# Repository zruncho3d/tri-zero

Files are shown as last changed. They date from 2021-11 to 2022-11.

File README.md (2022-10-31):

# Tri-Zero - a triple-belted-Z V0 mod

a Voron Zero mod to add Automatic Bed Leveling - under $100, in only a few hours.

**Make every first layer perfect** and never adjust a bed screw again!  :tada:   

Upgrade your V0, or build a T0 from scratch with an augmented V0 kit.  

#### **Now with a Plus50 size, which adds 50mm X and Y travel, to 170mmx170mm:**

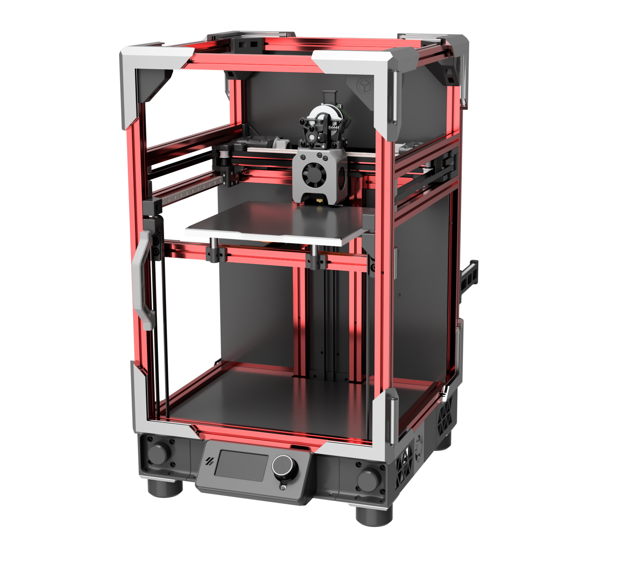
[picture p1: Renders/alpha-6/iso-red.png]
|  |
| - |
| T0 Plus50 with optional [BoxZero](https://github.com/zruncho3d/BoxZero) mod, Tecnologic-style [ZeroPanels](https://github.com/zruncho3d/BoxZero), and Mini 12864 display. |

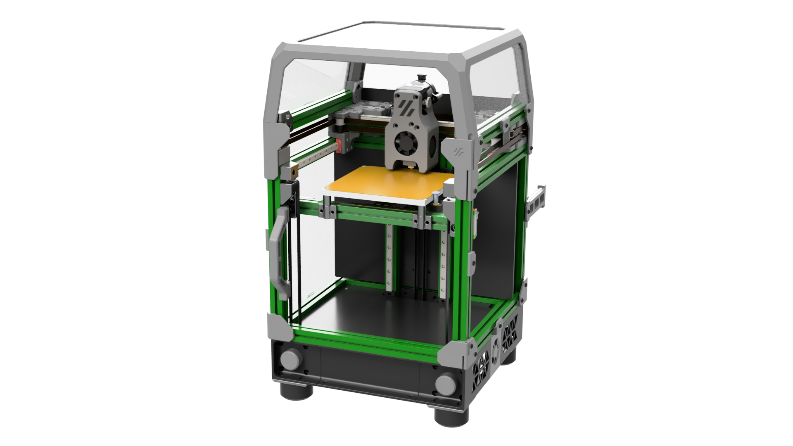
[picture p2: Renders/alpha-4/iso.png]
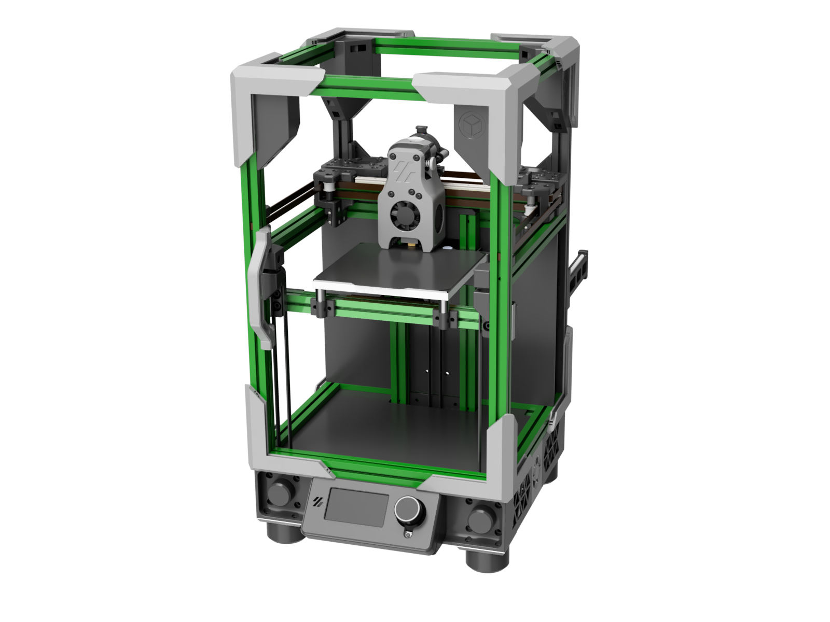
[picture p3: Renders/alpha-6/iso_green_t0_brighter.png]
|  | 
| - | - |
| T0 applied to V0 | T0 + [BoxZero](https://github.com/zruncho3d/BoxZero), [ZeroPanels](https://github.com/zruncho3d/BoxZero), & display.

### Why T0, vs other [Printers for Ants](https://3dprintersforants.com)?
* Less $, fewer failure points, and less potential for ringing than flying-gantry printers
* Faster Z motion compared to lead-screw printers, with no possibility of Z-banding
* Retains full space for electronics on the back
* Uses spare steppers you probably already have

*You don't even need to take the frame apart to do a V0 conversion.*

T0 is actively developed and community-supported, with over 20 builds completed, or in progress, as of October 2022.  Here are a few sample builds:

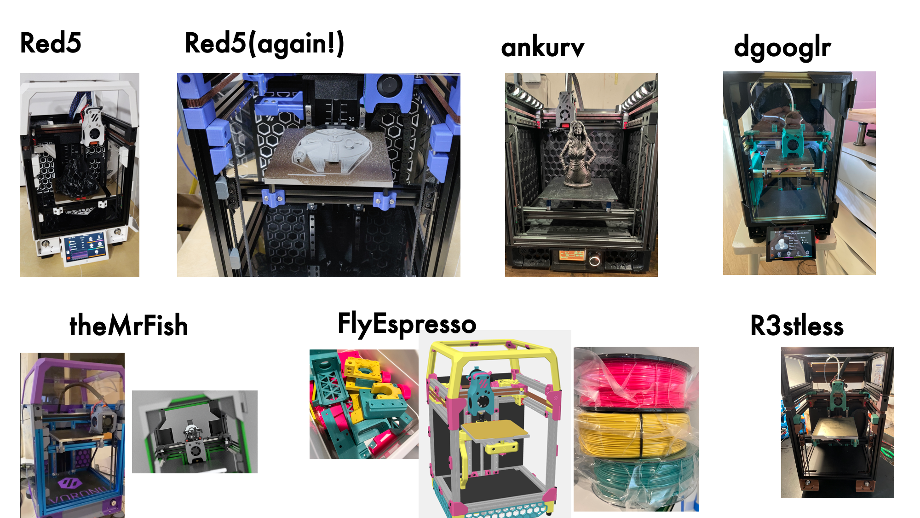
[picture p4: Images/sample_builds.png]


**Compatibility with the V0 ecosystem of kits, parts, and mods is a huge benefit**.

Plus, this mod pairs beautifully with the full family of Tri-Zero spinoffs:
* [BoxZero](https://github.com/zruncho3d/BoxZero) adds stability, easier sealing, and scalability for Plus50
* [ZeroPanels](https://github.com/zruncho3d/ZeroPanels) enables side panels to snap in/out in seconds, with an easy hinged top option
* [Dueling Zero](https://github.com/zruncho3d/DuelingZero) is a fully-boxed Tri-Zero with dual  gantries (!?!)

.. as well as [Double Dragon](https://github.com/zruncho3d/double-dragon), the IDEX V0 mod.

Join us on the [DoomCube Discord](https://discord.gg/doomcube) for any questions, comments, or just to see the latest dev activity.
*  Use `#tri-zero-forum` for support questions and build updates
*  Use `#tri-zero` for general chat and dev activity

Or, just straight to detailed docs:
- #### [Parts](PARTS.md): sourcing details
- #### [Instructions](INSTRUCTIONS.md): build steps, prep, and more
- #### [Plus50 size](PLUS50.md): sourcing and build notes for Plus50
- #### [FAQ](FAQ.md): Common questions, answered
- #### [Change](FAQ.md): Visual summary of past changes

## Overview and features

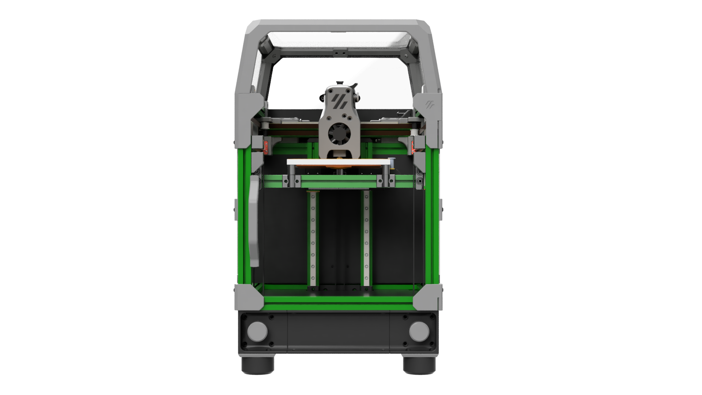
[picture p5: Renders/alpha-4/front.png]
Front
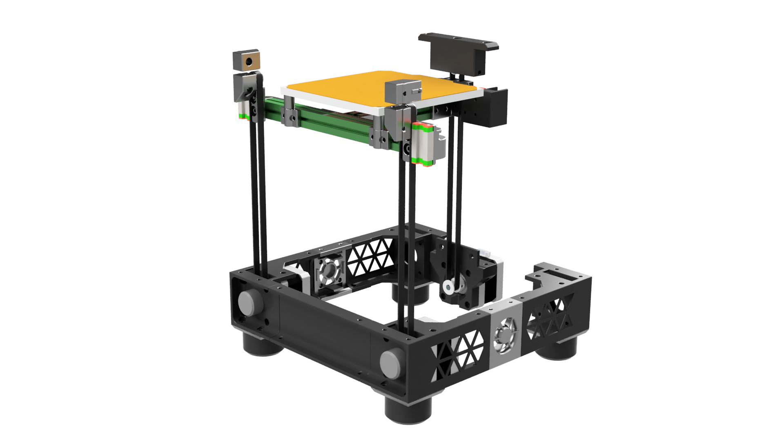
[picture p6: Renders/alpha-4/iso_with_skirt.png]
Iso with skirt
| Iso |  |   |
| - | - | - |

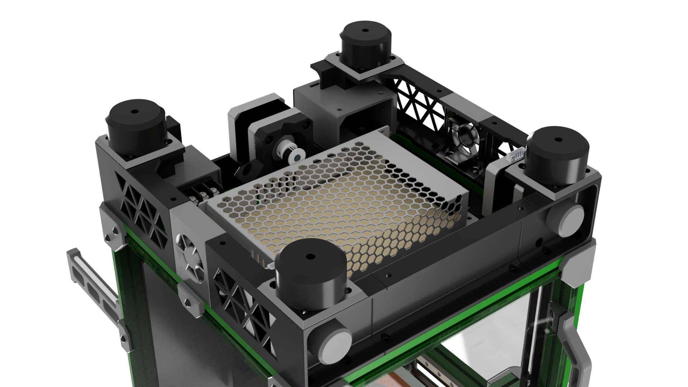
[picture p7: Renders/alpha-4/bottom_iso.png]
Bottom Iso
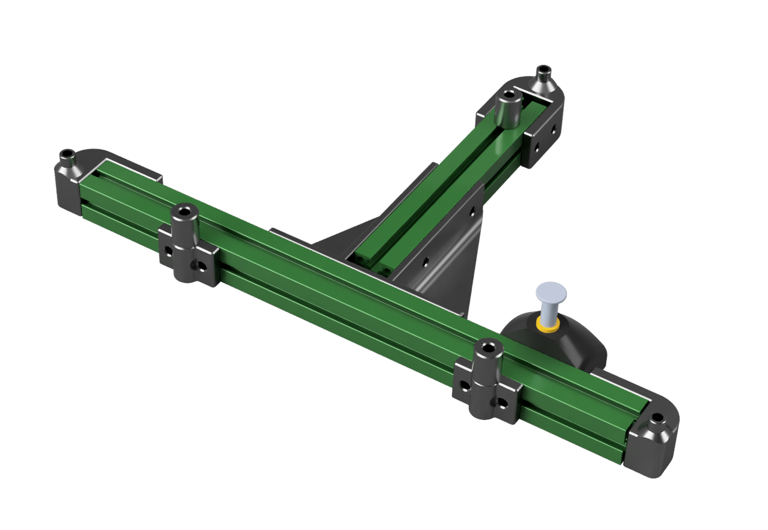
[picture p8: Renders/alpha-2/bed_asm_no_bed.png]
Bed Frame
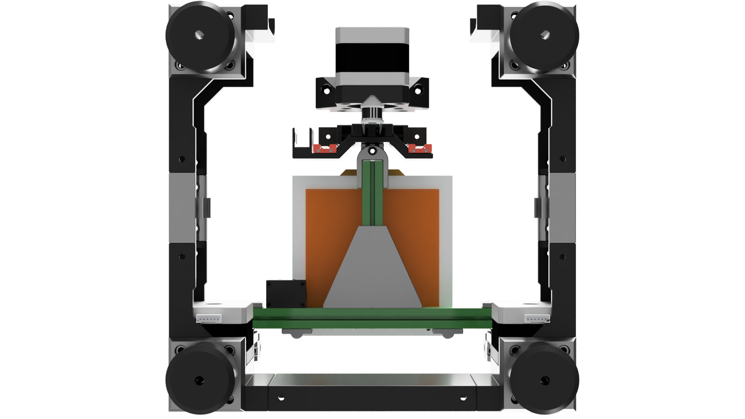
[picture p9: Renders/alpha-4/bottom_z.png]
Bottom Z
|  |  |  |
| - | - | - |

* Perfect Z layers, quiet motion, and great bed stability from 3 belted Z axes; no floppy cantilever here
* Reliable, stable Klicky-style bed probing with the [ZeroClick](https://github.com/zruncho3d/ZeroClick) detachable probe
* Optional rear endstop enables [automatic Z calibration](https://github.com/protoloft/klipper_z_calibration) and even auto-Z-offset for [IDEX](https://github.com/zruncho3d/double-dragon)
* Easy bed attachment and removal with built-in Wago mounts: 3 screws each
* Easy belt attachment and removal: fully tool-less
* Easy single-screw tensioning on all Z axes
* Easy to assemble: no hard-to-access screws or assembly-order nuances
* Your choice of display: 4.3" Touchscreen, Mini 12864, V0 Mini Display, or blank panel
* Supports large NEMA14 and mid-to-large NEMA17 Z motors
* Clean, minimal aesthetics with no-bridge, no-extreme-overhang parts

*This repo includes everything you need to build your own T0, including CAD and STLs for printed parts, as well as a list of parts:*

## Latest Release: Alpha-6

**There's never been a better time to deploy this mod.**

The community is growing.  20+ builds completed.  

With Alpha-6, the docs are vastly expanded and improved.  You can expect more good stuff to come, to make this mod  easier and faster to build.

**New in this release:**

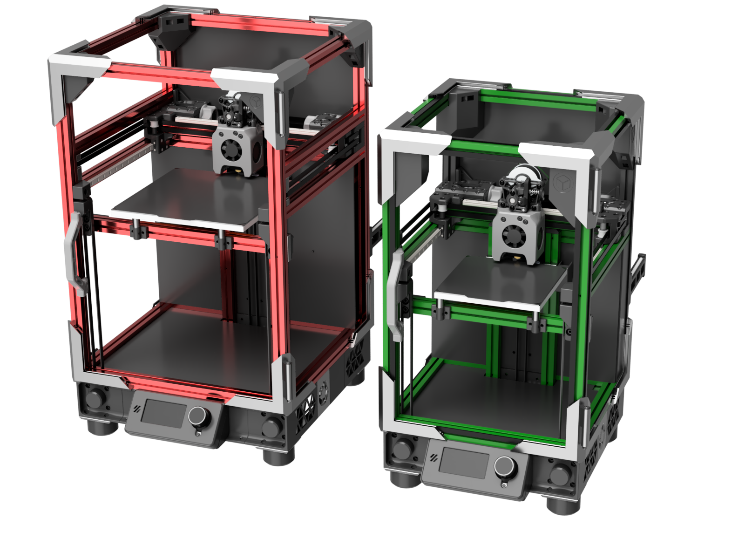
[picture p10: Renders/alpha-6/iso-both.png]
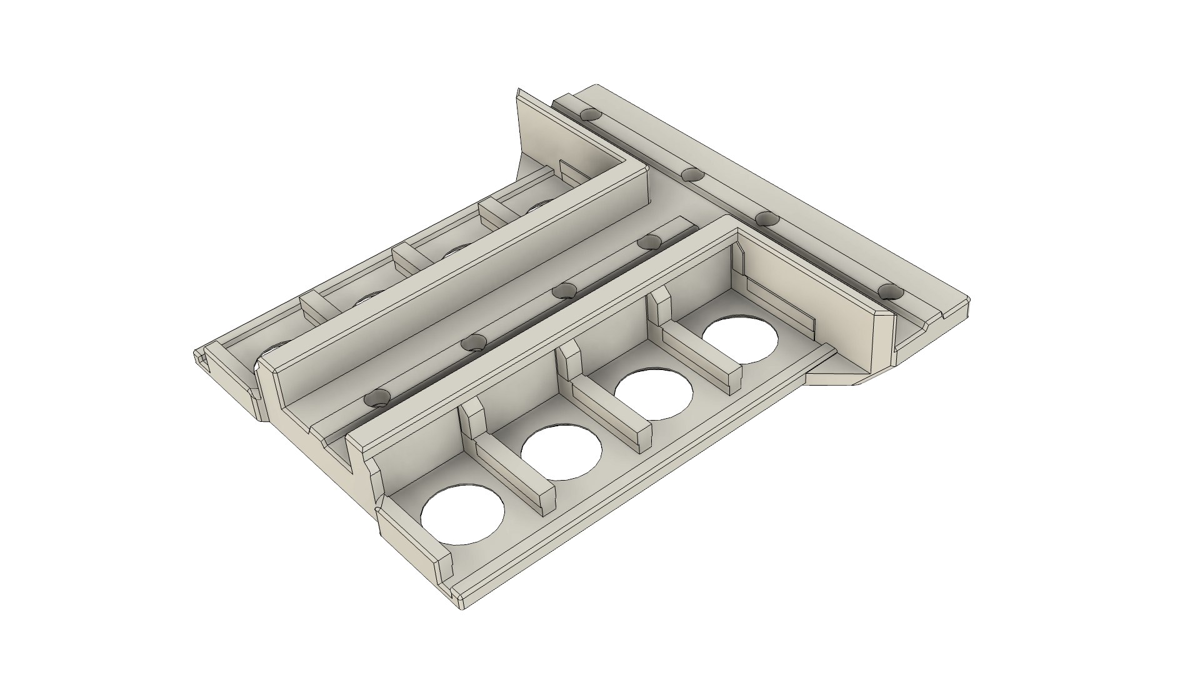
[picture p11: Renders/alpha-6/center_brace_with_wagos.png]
Iso with skirt
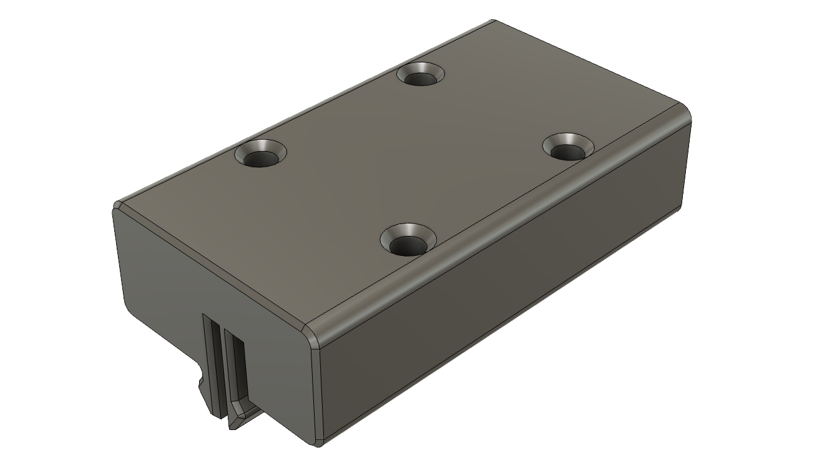
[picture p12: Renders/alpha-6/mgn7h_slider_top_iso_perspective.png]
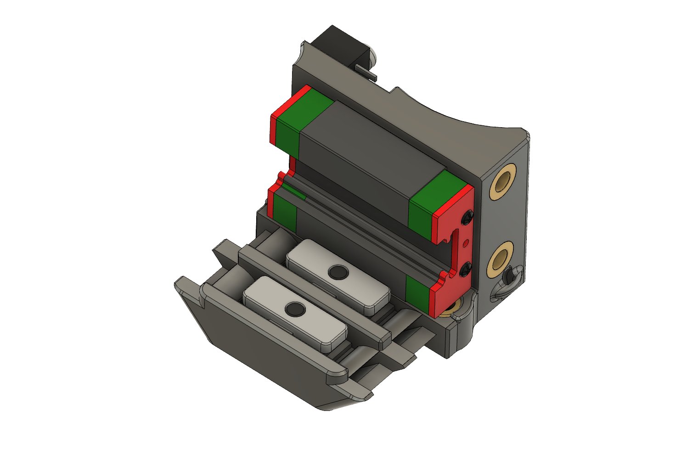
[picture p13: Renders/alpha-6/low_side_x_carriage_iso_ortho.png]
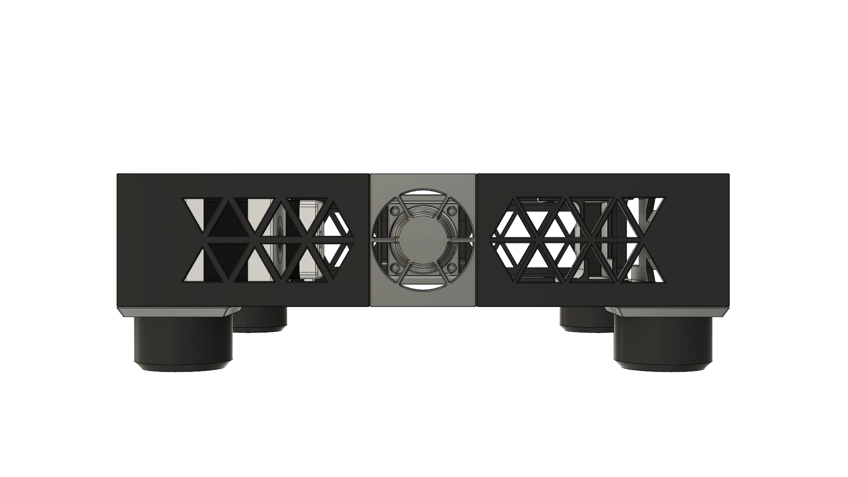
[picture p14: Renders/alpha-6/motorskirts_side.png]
Iso with skirt
|  |  |  |  |   |
| - | - | - | - | - |
| Plus50 Size | Integrated-Wago Bedframe | Rail-less Z Option | No-flush-cut carriages | 40mm Side Fans |

* **Plus50**, or **T0+** for short, is a new, larger, supported build size.  120x120 is good, but 170x170 is more usable, for little extra money.  T0+ can even be a cost-effective conversion for a V0, using 50mm extrusion chunks.  Shop the new [Plus Size](PLUS50.md) section for this year's newest model.

* **Bedframe with integrated Wago mounts**: Oh yes. The new "Connect 4" bedframe center makes bedframe attach/detach even easier, with up to 8 Wago connectors to support a bed heater, thermal fuse, optional AC ground, endstop, and thermistor wires.  Pop the Wagos in and out, toollessly.

* **Rail-Less Z Carriages**: Printed replacements for MGN7H rails that slide in an extrusion channel! Faster to install and saves money, too.  Used successfully on at least 4 builds at this point, including [Dueling Zero](https://github.com/zruncho3d/DuelingZero), so it's time to be more public about them.  *Currently considered experimental*, as the design is likely to change, and there is no long-term wear data on them.

* **No-flush-cut MGN9C carriage** Inspired by the [Double Dragon](https://github.com/zruncho3d/double-dragon) MGN9C mount; another T0 spinoff, first seen on [Dueling Zero](https://github.com/zruncho3d/DuelingZero).  No more one-time-use belts!

* **40mm fan skirt**: A potentially quieter option.

**Improved in this release:**

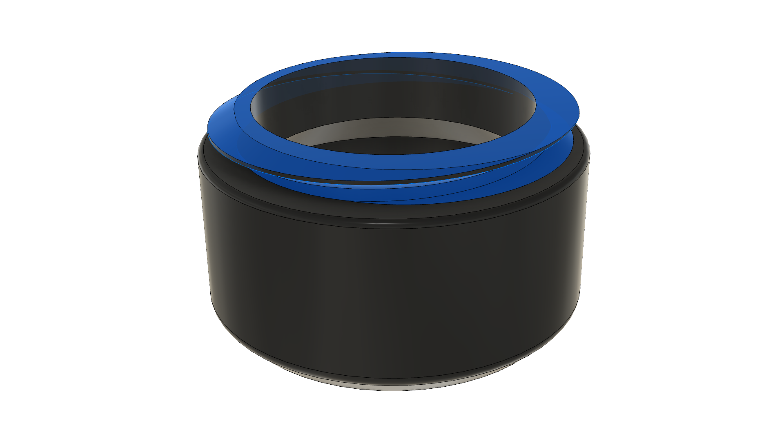
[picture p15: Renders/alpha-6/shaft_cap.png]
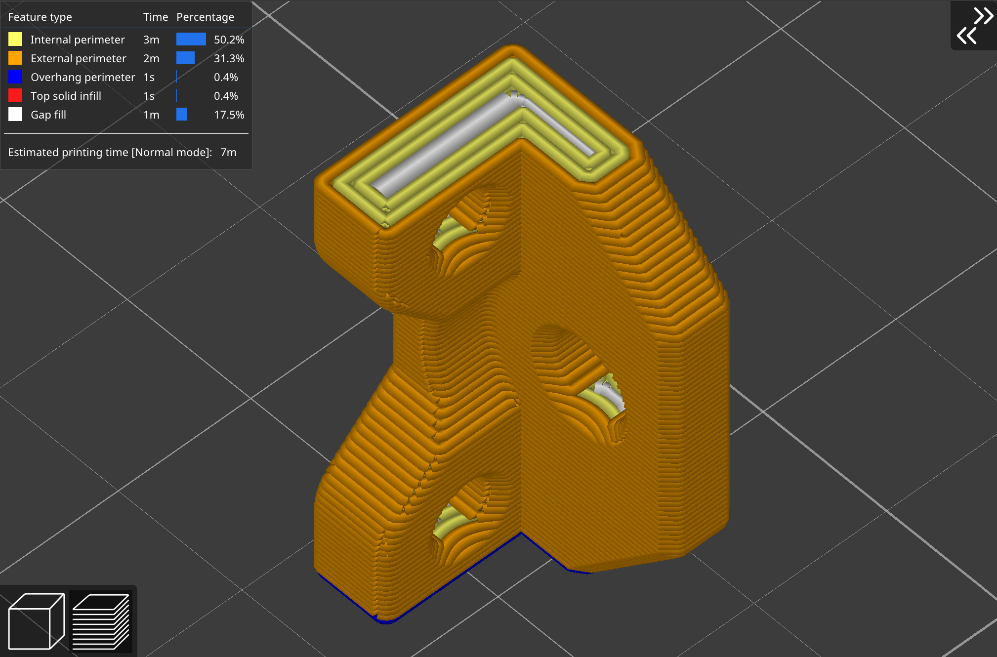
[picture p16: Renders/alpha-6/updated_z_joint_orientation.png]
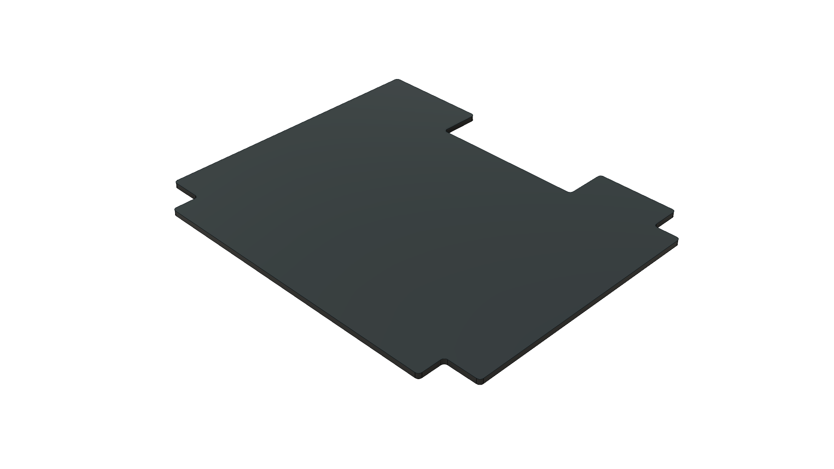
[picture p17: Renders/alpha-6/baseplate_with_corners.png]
Iso with skirt
|  |  |  | 600+ lines added! |
| - | - | - | - |
| Screw-in Shaft Caps | Updated Z joint orientation | Baseplate with corners | New docs all over |

* **Screw-in Shaft Caps**: These match updated MotorCorners; they'll never break now, with no clips in shear.  Much nicer.

* **Updated Z joint orientation**: Now printed vertically, to add strength in bending.  Should reduce the chance of breaking a $0.01 Z joint print upon head crashes.

* **Baseplate file with cutouts added**: Long-requested; saves the need to bust out your flush cutters or Dremel, if you're sourcing from scratch.

* **Docs**: Lots has been learned in the last year of T0, and now we have specific motor recommendations, config notes, tips, build steps, and an FAQ.  More visual, more engaging.  No proper manual yet, but this gets us halfway there.

Thanks to everyone who contributed to this release by testing parts!  You know who you are, and you'll get the ping-for-test again, I assure you :smile:.

I'm behind on reviewing GitHub pull requests, and that's up next: to make your mods more visible.

## Prior Changes

Prior changes (alpha-5, alpha-4, ...) are now noted in the **[visual changelog](CHANGES.md)**, which explains how T0 has evolved and walks through the interesting parts.

### Build Options: an Overview

No two builds are likely to be identical, and that's OK.  You're a smart, independent builder, and here you get to choose amongst the options to match your priorities and budget.  Next up is a quick overview, with the shared elements after.

#### Least-cost Stock-size Option: "starving student special" conversion - $0-$75

**Performs well, at minimum cost.**

Buy 3 small NEMA14 motors (< ~$30), print some sliders, and keep using your MGN7H X rail.  Buy some pulleys ($5), belt ($5), and fasteners ($10ish).  Buy a low-cost 2-4 driver board ($25).  Potentially $0 if you have the parts lying around from other printer, including magents and a switch for ZeroClick.  Sure, the rear bed joint might occasionally drop when the power cuts, and the sliders require a little bit of tuning, but once the printer rehomes, you're good, and the Z motion quality should match real rails.

#### Premium Model, 120x120: ~$110

**Performs the best.**

Might as well upgrade your X rail to MGN9C while you're at it ($15?), to  reduce toolhead flop.  Use beefy 48mm NEMA17s (~$45), and for rails, add one MGN7H to go with the one you just freed up ($15).  Otherwise the same.

#### Least-cost Plus50 BoxZero conversion: ~170x170: ~$150 to ~$200

You're also looking at a new K3-style or Prusa-Mini-style bed/magnet/flexplate ($35+), additional extrusion pieces ($30), new 200mm XY MGN7Hs and a 200mm MGN9C ($50), plus new longer XY belts ($10).  Yields a bit of extra Z travel too.

The price point is maybe $50 less if you're scratch-building and can leave out the Z rails, or you sell all the rails from your kit to someone who is scratch-building.  More details in the Plus50 section.

#### Premium Model, ~170x170: ~$200-$300

Move 4x MGN7H rails to Z, for ~130mm Z travel.

Optionally, add new clear ($20) and solid panels ($20).

Optinally, add a top-grade bed, like one from Mandala Rose Works meant for a Salad Fork.

Optionally, go for taller panels, taller BoxZero corners, custom frame, and 200mm MGN7H Z rails, to get a 170x170x170 build cube.

### Additional Credits / History

This printer is inspired by lessons learned while designing, building, and iterating on [F-Zero](https://github.com/zruncho3d/f-zero), a Voron Zero mod to add automatic calibration to a V0. Initial versions of T0 (alpha-1 and alpha-2) used F0 Z units with pulley reductions.  Now, T0 has moved to direct drive for Z, and the two designs now have almost no shared parts.

The [Buildlog Gdoc](https://docs.google.com/document/d/1kADhQN-p30GZuGi_6izB4IUN-McIifvLVtg8yTzIAgo/edit#) has historical details and links to early versions there.

The tensioner part derives from [MCMBen's Block-and-Tackle Z for V0](https://github.com/Fleafa/VoronUsers/blob/master/printer_mods/MCMBen/Voron0_Block_and_Tackle_Z_Belt/STLs/%5Ba%5D_tensioner_v1.stl) - Zruncho prints this vertically for clean surfaces, but make sure you have good layer adhesion.

The 4.3" Waveshare Touchscreen mount is based on Jeoje's great Voron2.4 [Touchscreen mod](https://github.com/VoronDesign/VoronUsers/tree/master/printer_mods/jeoje/4.3_Inch_Touchscreen_Mount).

The Mini 12864 Display mount is based on Gola's [V0 Trident Skirt Mix](https://github.com/VoronDesign/VoronUsers/tree/master/printer_mods/golas/v0-trident-skirt-mix).

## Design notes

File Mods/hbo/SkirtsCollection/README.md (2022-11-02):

# Collection of Tri-Zero Skirts

This is a Collection of skirts for the try-zero with some additional features.

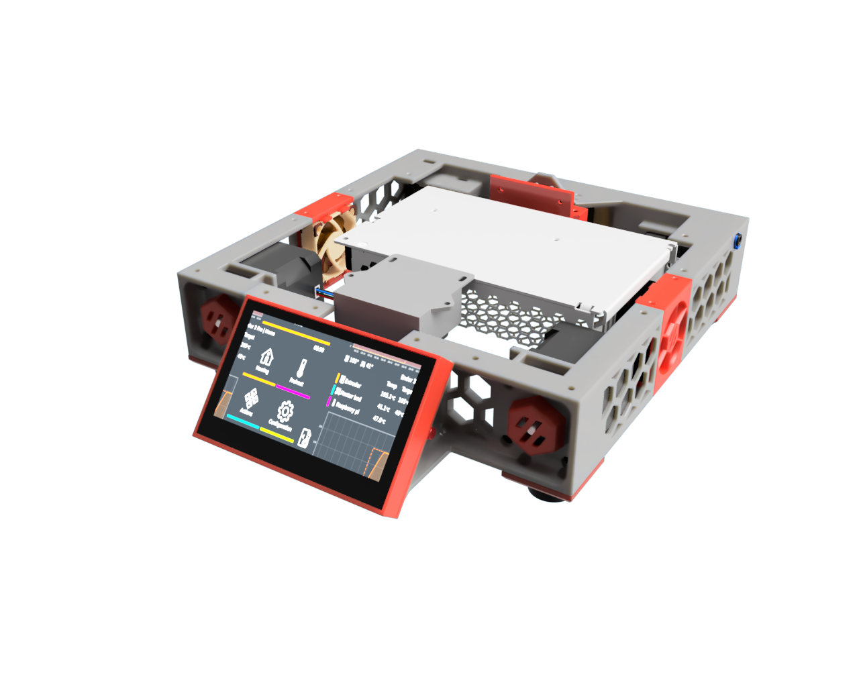
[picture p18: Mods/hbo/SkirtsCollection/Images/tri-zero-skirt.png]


Right now, there are 2 variations for the skirts and one common rear and common fan mounts.
To start with the rear ..

## Rear Skirts

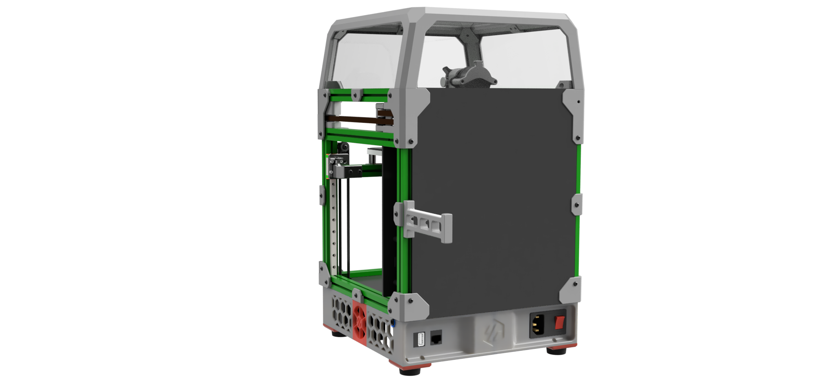
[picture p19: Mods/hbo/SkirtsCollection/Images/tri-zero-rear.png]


The rear skirts match all the different front skirts and have the following features

- integrated power inlet mount. To be used with the "standard" v0 power inlet
- 2 keystone mount points to get access to the raspberry pi ports
- Bowden clip mount point. Designed for the E3D style bowden clips. This allows to push the filament and not the tube from the outside. Read for the ERCF :)

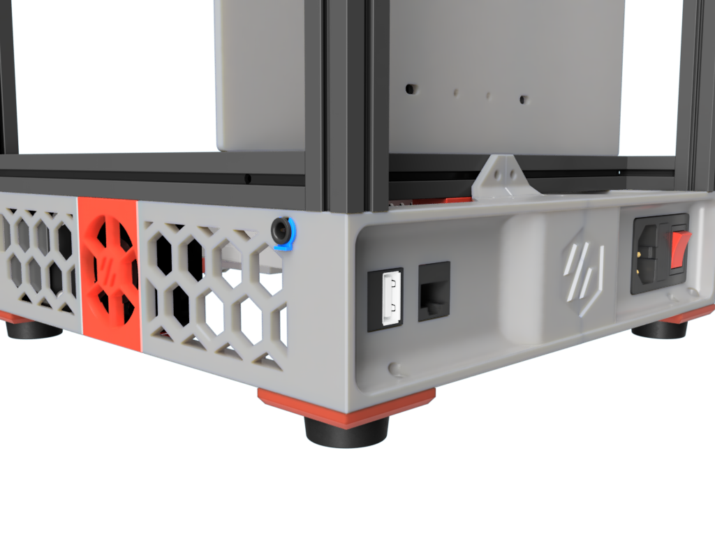
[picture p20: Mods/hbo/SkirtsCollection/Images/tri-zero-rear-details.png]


## Fan Mounts

Option: The fan mounts have clips to hold 40x10mm or 40x20mm fans.
If you go with a 20mm fan make sure to order one with a central rib, like the fans from creality.

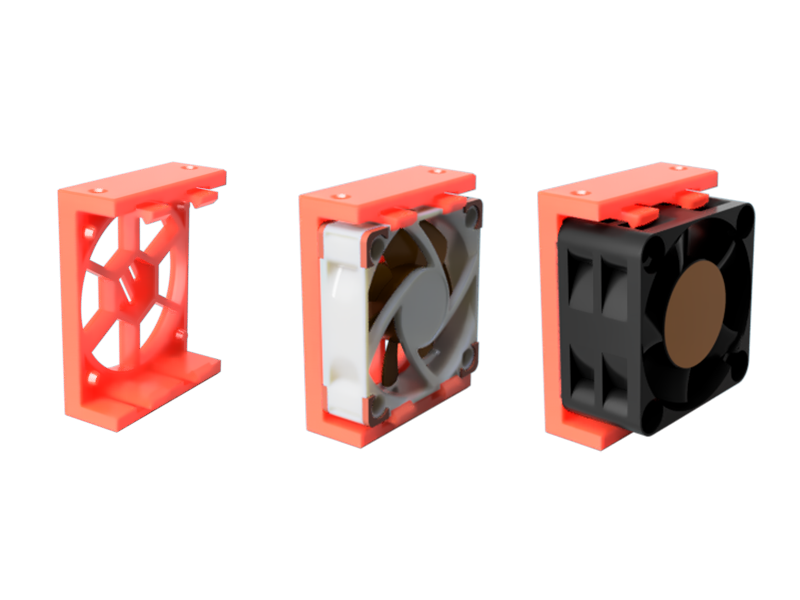
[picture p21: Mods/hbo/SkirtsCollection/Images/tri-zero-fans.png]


# Skirt Options

The front skirts are designed for Nema 17 motors up to a max size of 39 mm in length.

Note that there are two front covers for the GT2 pulleys. One for NEMA's with a shaft of 20mm and one for NEMA's with a 24 mm shaft.

## 1. Headless

This version is intended for users that like to run the tri-zero in headless mode i.e. without display

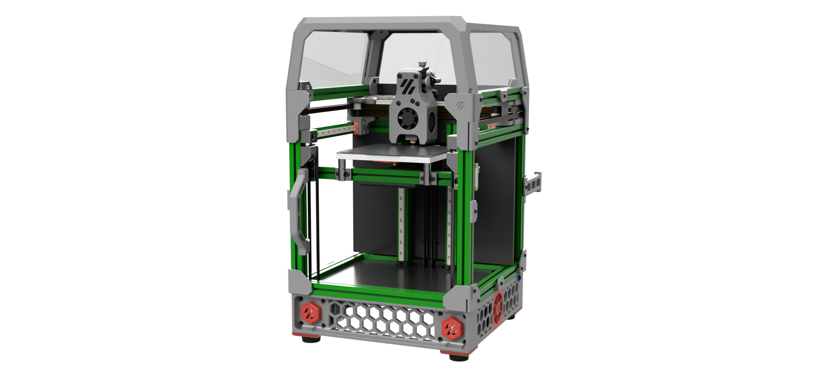
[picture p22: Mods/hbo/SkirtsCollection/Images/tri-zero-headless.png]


## 2. Waveshare 4.3" Display

This version is designed for the Waveshare 4.3inch Capacitive Touch Display for Raspberry Pi, DSI Interface
The mounts are designed to bolt on the frame and display with original screws from the back.
Therefore similar 4.3 inch display might not work without modifications
I'm using a 60cm DSI cable to connect the display with a Raspberry PI back on the back of the V0 
(a Raspberry Pico mount mod is in preparation)

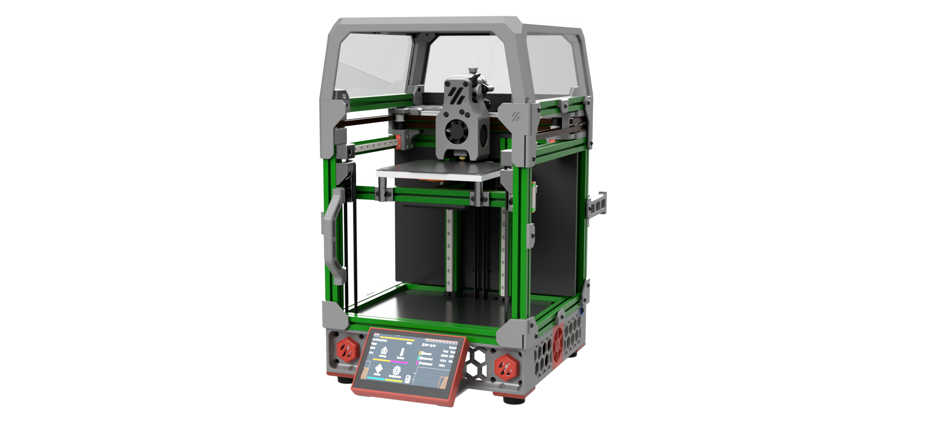
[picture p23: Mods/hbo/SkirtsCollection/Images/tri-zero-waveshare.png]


### Reset / Emergency switch
The front display mount also provide a mounting option for a reset or emergency switch.
I'm using this switch to reset a BTT PSU relays. 

The switch in the cad is a standard 7mm momentary switch that is easy to source even from local providers.
Make sure to get a Normaly OPEN (NO) switch if you plan to use it with the BTT PSU Relays.
(A Relays mount and firmware configs are in preparation)

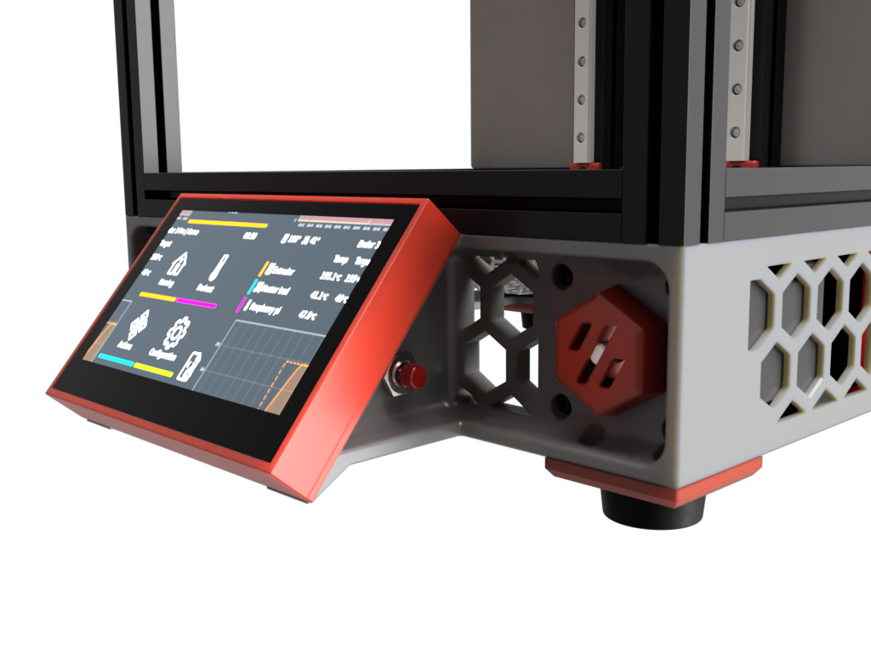
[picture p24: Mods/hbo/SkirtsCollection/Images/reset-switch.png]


# Printing

This mod is based on my design for the V0 and Double Dragon / Wasp printer.
The core design went to many iterations (and spools of filament) to optimize printability and tolerances for keystones, power inlets etc.

I printed the motor corners to check the design but I have not yet built a printer with them. So please provide feedback if you run into issues or confirm the design.

All parts print with standard Voron print setting without any supports.
All parts fit on a V0. However, the max out the build volume on the z axis.
If you need to print on a V0 make sure that your bed springs are really stiff by adding more tension with washers etc.
I had some problems getting nice parts out of the V0 due to the nozzle moving the part due to flex on the bed springs.

# BOM Notes

Recommended Nema 17 Motor: https://www.omc-stepperonline.com/de/nema-17-bipolar-1-8deg-26ncm-0-4a-0-4a-12v-42x42x34mm-4-draehte-17hs13-0404s1

Waveshare Display:  https://www.waveshare.com/4.3inch-dsi-lcd.htm

Rubber Feet: There are many options. The one in the CAD are these ones here https://de.aliexpress.com/item/1005004478863418.html

7mm Momentary switch:  https://de.aliexpress.com/i/32711341102.html

40x20mm fan:    https://de.aliexpress.com/item/1005002920453385.html

# CAD  Notes

The CAD includes all variants in one file.
You need to show/hide the version you like to work with

# Credits

Thanks to zruncho for all his efforts he puts into the printers for Ants.
It's inspiring for a lot of us!

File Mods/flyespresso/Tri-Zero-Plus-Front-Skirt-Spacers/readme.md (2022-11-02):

# Tri-Zero Plus: Front Panel Spacers
#### _For Tri-Zero Plus! Not needed for standard/V0 conversions_

This is a simple additional flair piece for the front, that will cover any gaps for whatever front you choose, i.e. waveshare as shown below. Blue highlights the additional pieces.

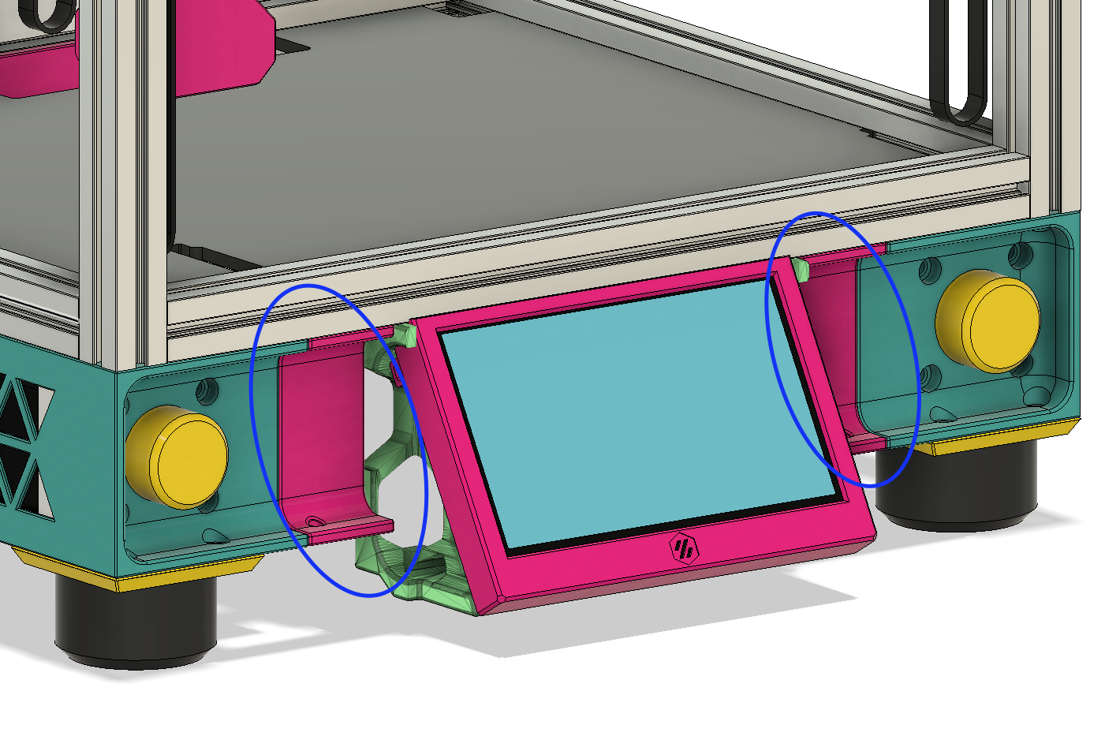
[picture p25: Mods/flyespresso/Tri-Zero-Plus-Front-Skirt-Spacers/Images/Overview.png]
Overview


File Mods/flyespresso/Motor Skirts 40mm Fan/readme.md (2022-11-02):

# 40mm Fan Motor Skirt Adapters
## _For Tri-Zero & Plus!_
This mod is made with Noctua 40mm fans in mind but should work for any 40mm fans, requires inserts.

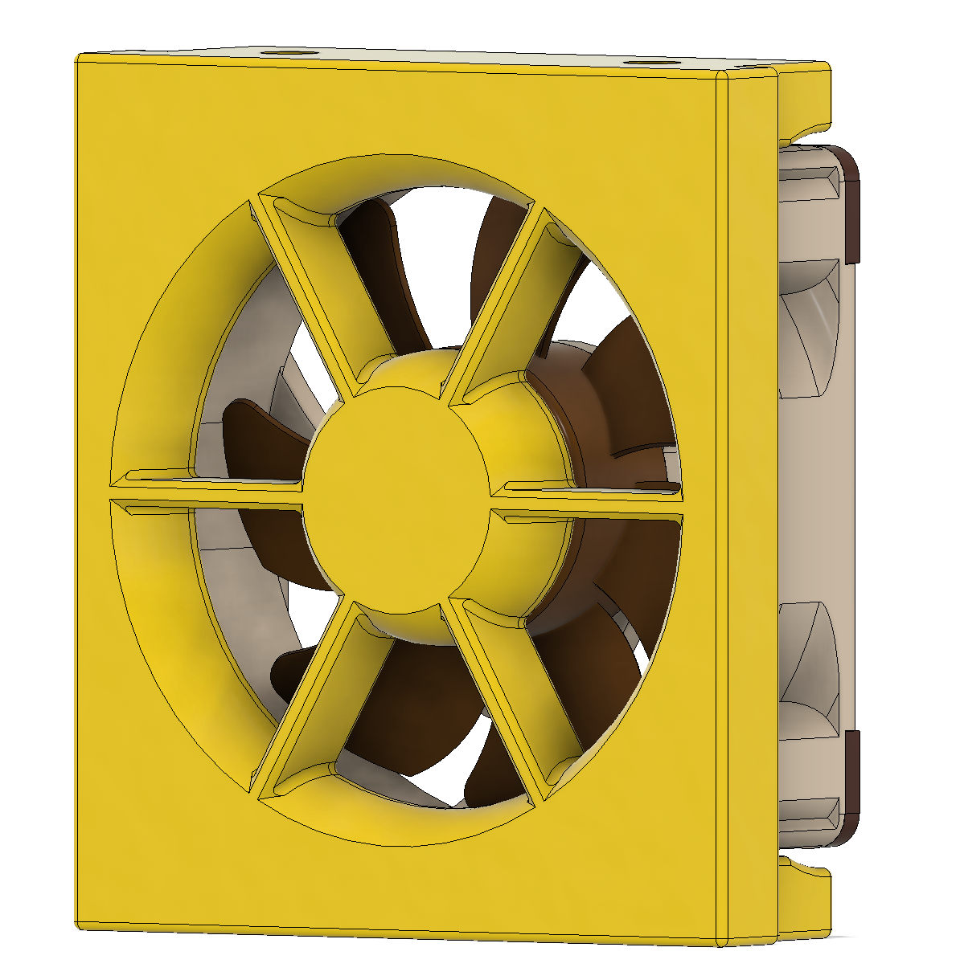
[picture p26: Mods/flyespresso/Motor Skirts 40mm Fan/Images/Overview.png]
Overview

Note that the holes to connect to the frame have a little overlap to the main body--that's fine as you can push the screw past that and then it acts like a captive screw. This way lot easier to instal! It's in the below images in Green. Red is where you will need heat sets (x4) per fan. See here:

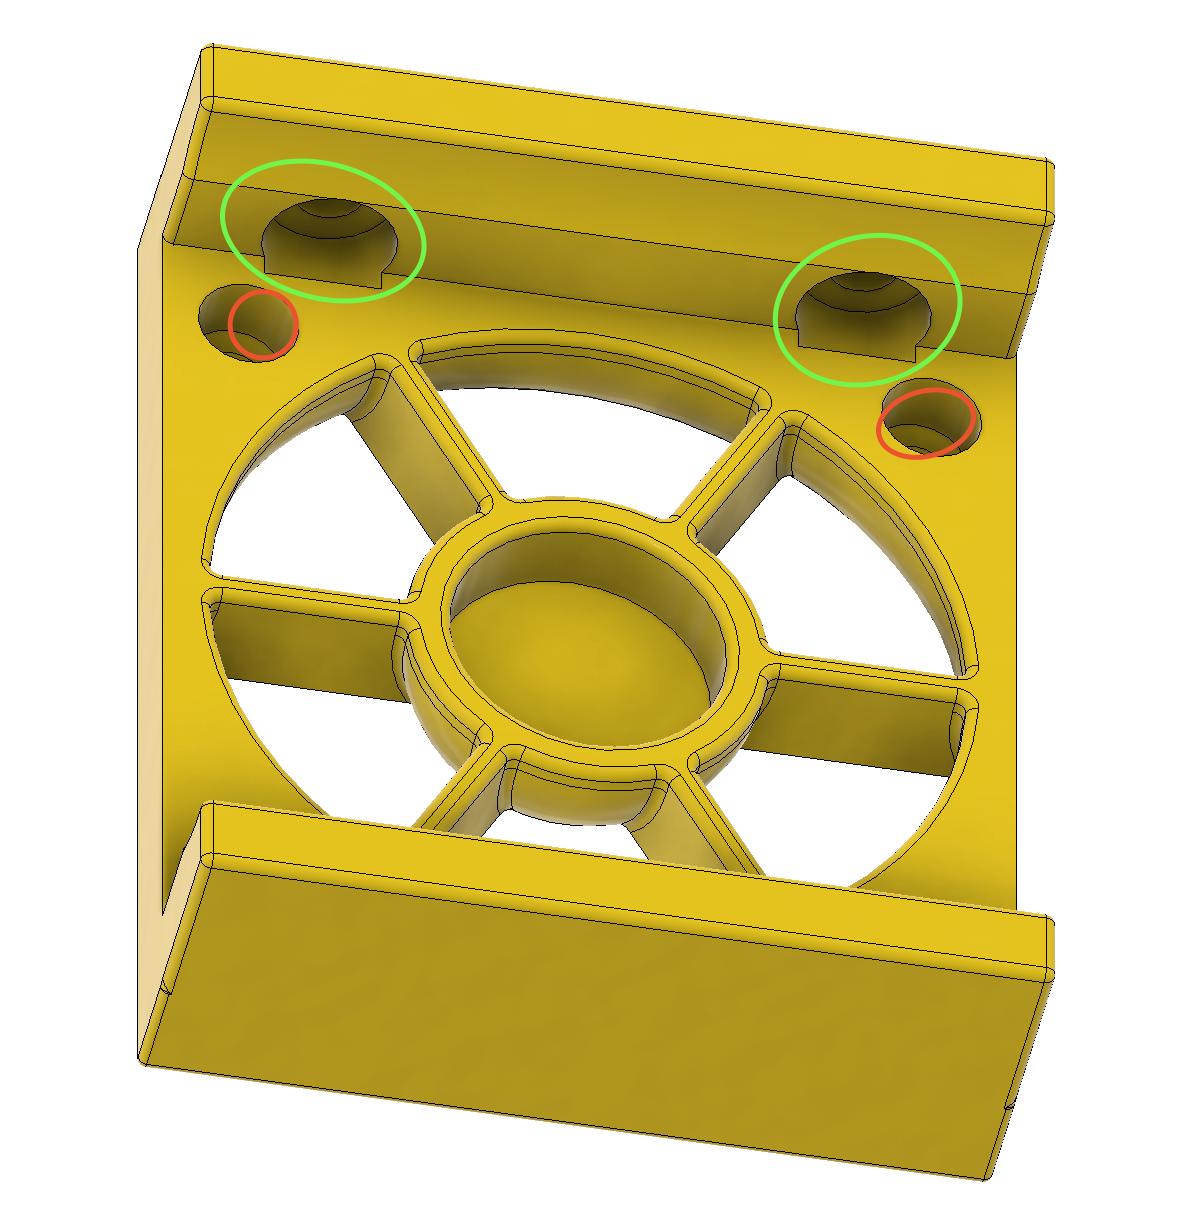
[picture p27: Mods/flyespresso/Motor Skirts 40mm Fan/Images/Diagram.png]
Diagram


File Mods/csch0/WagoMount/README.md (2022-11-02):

# Overview

Attach Wago 221-412 to your tri-zero bed.

Idea taken from this mod for the v0: https://github.com/VoronDesign/VoronUsers/tree/master/printer_mods/deepfriedheroin/v0_bed_wagos

## BOM
* 1x M3 8mm
* 1x M3 Nut
* 4x M3 6mm
* 4x M3 Heat inserts (from the V0 BOM)
* 6x Wago 221-412

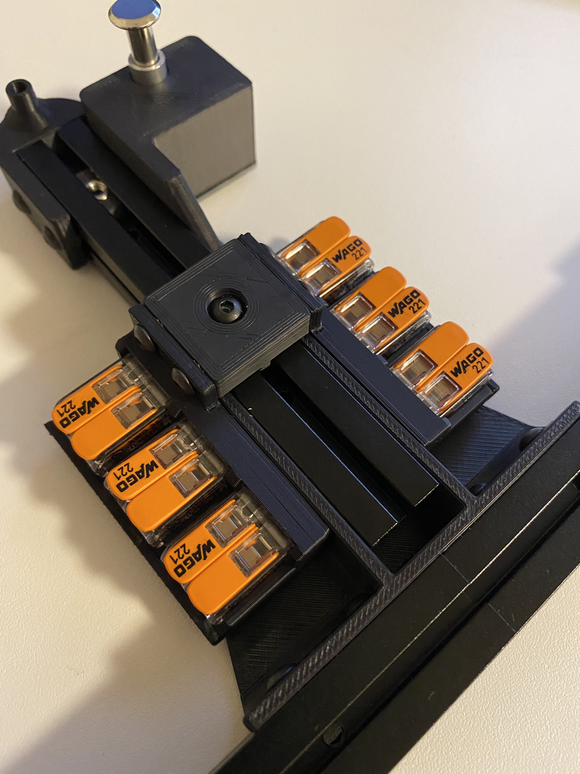
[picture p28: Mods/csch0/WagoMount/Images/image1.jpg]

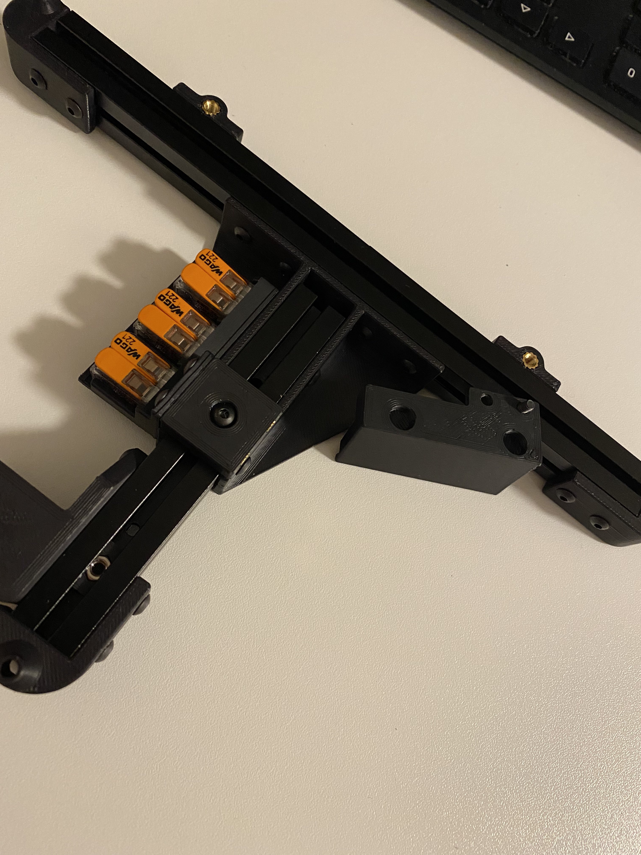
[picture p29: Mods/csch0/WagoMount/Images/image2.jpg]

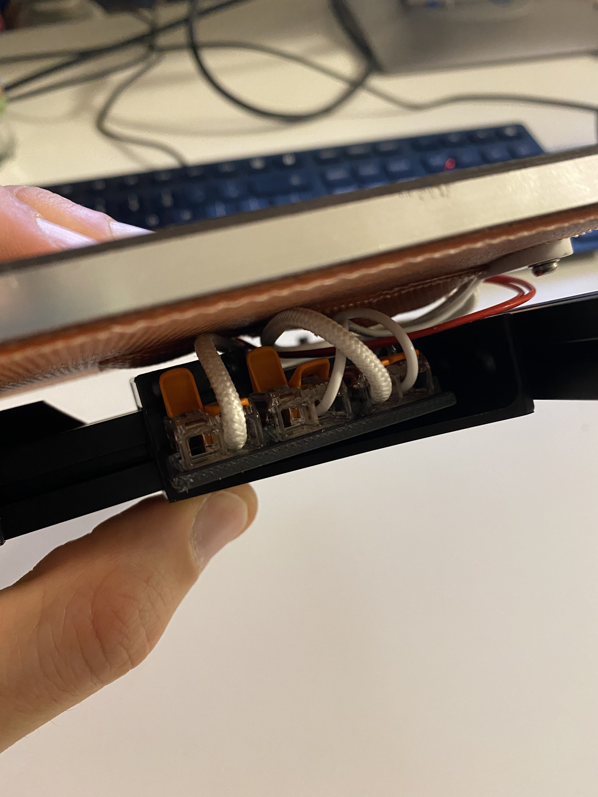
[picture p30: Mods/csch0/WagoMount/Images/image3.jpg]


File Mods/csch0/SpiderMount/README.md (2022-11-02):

# Overview

Mount for the spider mainboard, supports the [Wire Fingers](https://github.com/zruncho3d/double-dragon/blob/main/STLs/Optional/Wire_Fingers_x6.stl) created by [zruncho3d](https://github.com/zruncho3d).

## BOM
* 4x M3 6mm
* 2x M3 8mm
* 6x M3 Heat inserts (from the V0 BOM)
* 6x [Wire Fingers](https://github.com/zruncho3d/double-dragon/blob/main/STLs/Optional/Wire_Fingers_x6.stl)

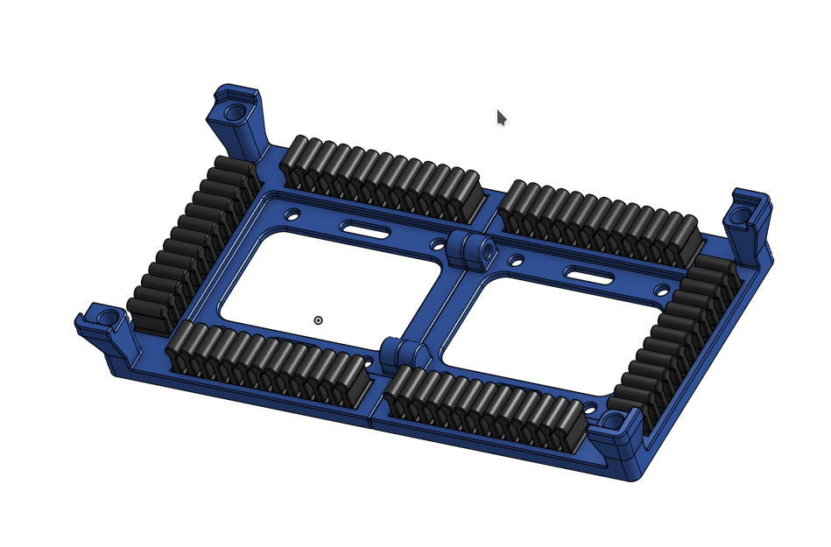
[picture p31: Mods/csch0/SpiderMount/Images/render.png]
render


Installed it looks like this on my tri-zero.

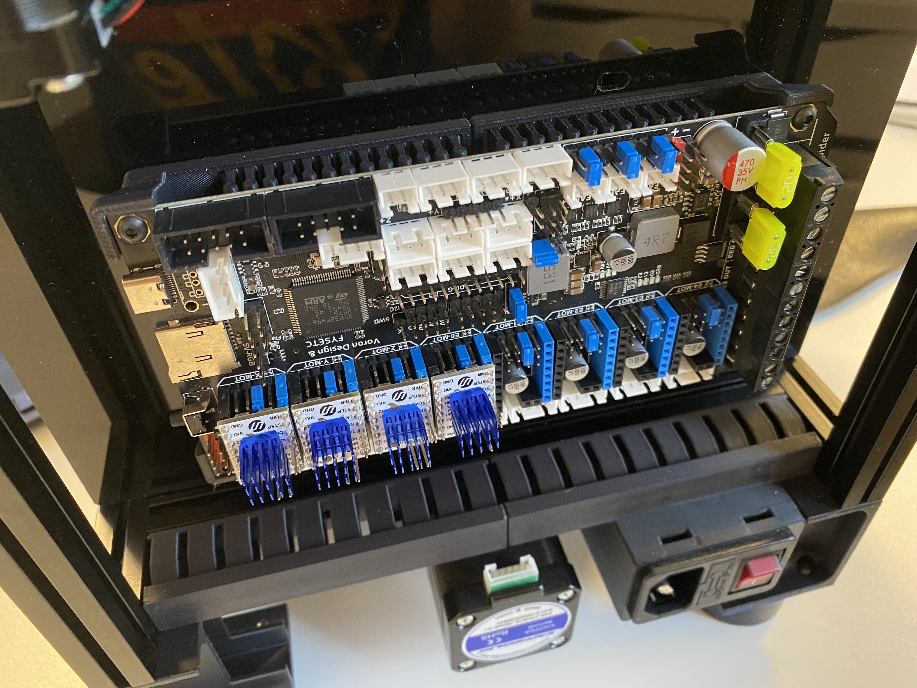
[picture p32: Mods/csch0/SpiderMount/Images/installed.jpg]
installed


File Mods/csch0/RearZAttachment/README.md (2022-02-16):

Rear Z Attachment, fixed cable chain with crews and add zip tie support.

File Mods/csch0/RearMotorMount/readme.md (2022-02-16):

Different mount for nema17 I used stepperonline 17HS15-1504S-X1.

This is the stepper motor with a 2mm spacer.

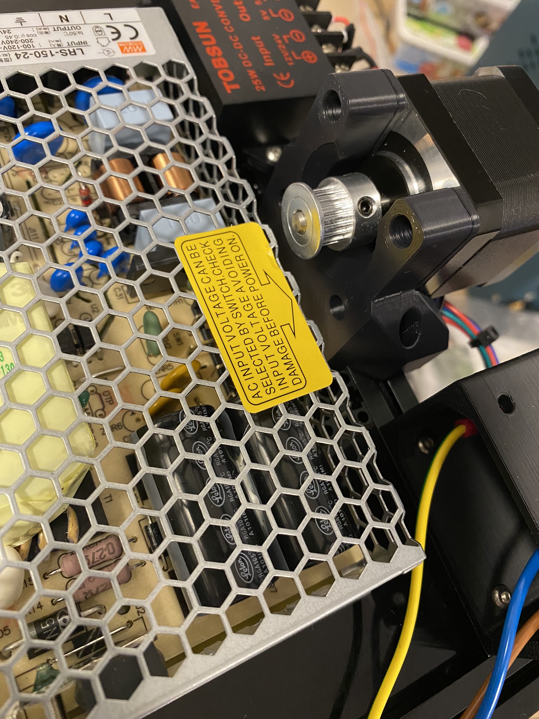
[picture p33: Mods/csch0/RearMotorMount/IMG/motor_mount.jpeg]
motor_mount


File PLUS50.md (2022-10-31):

# Plus50

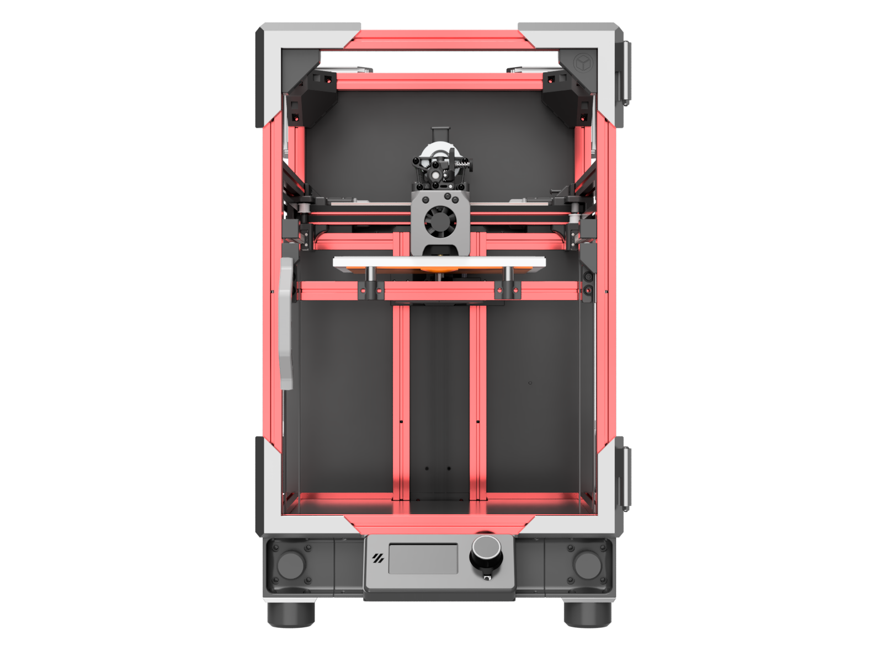
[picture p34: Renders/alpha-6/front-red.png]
|  |   |
| - | - |
| Front | Iso |

Plus50 adds 50mm of X and Y travel.  

At a high level, that parts are mostly the same, including V0 and the T0 gantry and toolhead.  A few extra parts in the [Plus50](STLs/Plus50) directory are needed to widen the rear umbilical, place the bed optimally, and span the wider skirts.

The Plus50 size just feels right for [BoxZero](https://github.com/zruncho3d/BoxZero).  While you *could* use existing, available Double Dragon parts to extend a tophat, it's not worth it.  Too many parts to print, too many fasteners, and too many areas to seal.

We'll assume that you go [BoxZero](https://github.com/zruncho3d/BoxZero) if you go Plus50, even if that's not strictly necessary.  The BoxZero corners add rigidity, easier sealing, and easier mounting.  You won't regret them at either size.  If doing 400mm verticals, use `Top_Corner_Mini_x4.stl`, unless you really want extra space for Z.

For Z, you have two choices:
- **(1)** Keep Z travel the same, at 120mm.  Go with a 50mm taller frame, mostly retaining V0 frame parts and reusing XY rails for Z axes.  This setup gives needed space for umbilical clearance.
- **(2)** Add 50mm Z travel with 200mm MGN7H rails to match the XY increase and also add umbilical clearance.

In both cases, printed sliders are an option.

## Parts Needed

### Frame: New-build-specific
You'll need the following extrusions:
* 13x 250mm (horizontals, including bedframe)
* 4x 400mm (for verticals)
* 1x 100mm (for rear of bedframe)

### Frame: V0-conversion-specific
For reference, a stock V0 frame has:
* 16x 200mm
* 3x 100mm

To convert, you'll need added extrusion content.  We'll assume you want to put the colors in the front, and can use m3 set screws to connect extrusions with stock 50mm chunks, per the [method noted in BoxZero](https://github.com/zruncho3d/BoxZero#frame-and-corners), using the extrusion wrench available there to avoid marring the extrusions.  

Here's what they look like on Dueling Zero, in the back:

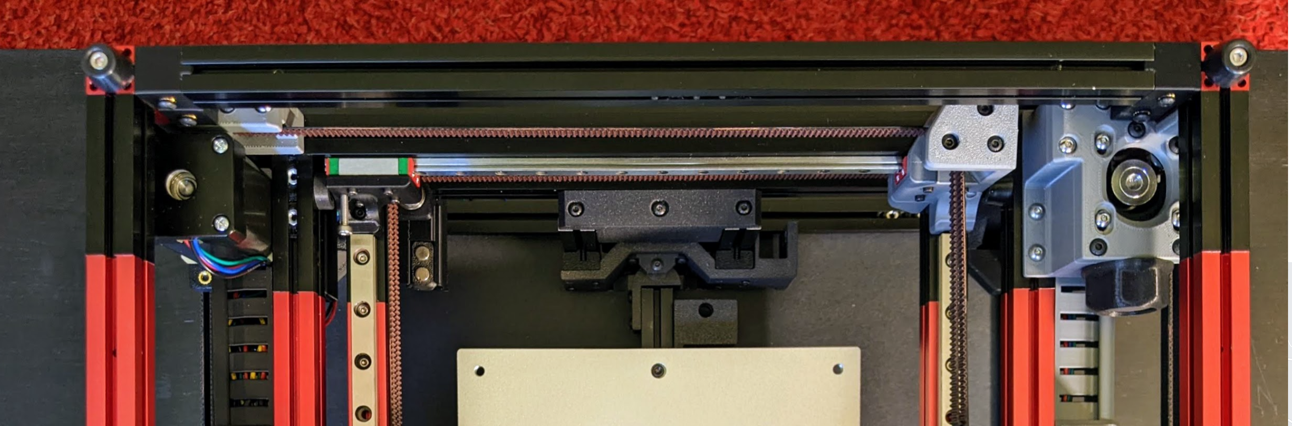
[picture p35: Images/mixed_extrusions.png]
Iso


In practice, this method looks great, even if the rear is black or silver; Technologic-style ZeroPanels will cover up the extensions in the front anyway, so you'll never see them.

A suggestion:
* Front Verticals: 2x, 200+200, joined (color)
* Side Horizontals: 6x, 50+200 joined (color)
* Front Horizontals: 2x, 50+200 joined (color)
* Bedframe Front: 1x, 100+50+100 joined (color)
* Bedframe Rear: 1x, 50+100 joined (color or no color)
* Rear Horizontals, 3x 50+100 joined (no color)
* Rear Verticals: 2x 200+200 joined (no color)

This has black for everything in the back, with 50mm chunks on the black part, and color in the front; yes, you will have some colored extrusions left over.  IF you have the dark bits forward, it will save the need for drilling 4 of the holes that connect to X crossbars, but that's about it.  And if you make the rear verticals colored, you'll have 50mm of floating black bits, for better or worse.

So, you need:
* 10-ish 50mm chunks: [MBXL Amazon link for 8x50 + 4x100](https://www.amazon.com/gp/product/B06XJ4T6TW)
* 7-ish 200mm chunks: [MBXL Amazon link for 4-pk](https://www.amazon.com/MakerBeam-XL-Anodized-200x15x15mm-Pieces/dp/B06XHQH9WH)

None of this is set in stone.  You should choose extrusions to match your color desires and ability to chop existing extrusions.  You should place the specific extrusions as much as possible in places where you won't need to drill too many holes.  But good news!  Your original V0 drilling guide will work just fine here.

No frame pic yet showing 50mm chunks, but hopefully these words make it clear.

### Common: New or Conversion

**Z Motors**:

Go for large NEMA17 motors, 40mm body length or larger.  You want the strongest motor possible to resist motion when unpowered, given that the bedframe is much heavier with a larger bed and longer extrusions.

**Larger Bed**

Travel motion goes up to 170x170 in size, with 5mm reserved for a nozzle endstop if present, so something near this range is best.   Something smaller (like 160x160)  leaves space for an endstop Z switch, purge bucket, and/or even a nozzle wiper.  Something larger (like 180x180) leaves clearance at the ends for a more consistent bed temp, as well as heats up the chamber faster if a larger bed fits.

Three main choices here:
* Voron-style MIC6 1/4" Al bed with magnetic tape, in Annex-K3-size, with AC or DC heater
  * [Funssor](https://www.aliexpress.com/item/3256803530287164.html)
* Prusa Mini 190x190-ish thick circuit-board with embedded magnets, DC typically
  * [Fysetc](https://www.aliexpress.us/item/2255800748491824.html)
* Mandala Rose Works-style bed with embedded magnets, with AC or DC heater
  * [MRW Micron 185 magbed](https://mandalaroseworks.com/collections/micron-185)
  * [MRW Micron 160 magbed](https://mandalaroseworks.com/collections/micron-160mm)

**Panels**

Assuming 400mm blind corners:

| Category | Part | Qty | Notes | Link |
| - | - | - | - | - |
| Panels | 262x382x3mm panel | 3 | Side and front panels, clear acrylic
| Panels | 262x262x3mm panel | 1 | Top panel, clear acrylic
| Panels | 262x382x3mm panel | 3 | Rear panel, ACM or ABS
| Panels | Plus50 DXF  | 1 | Baseplate, ACM or ABS

**Longer XY rails**
* +50 --> 1x 200mm MGN9C (for x, TODO link)
* +50 --> 2x 200mm MGN7H (for y, TODO link)

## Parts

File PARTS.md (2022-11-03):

### Parts List (vs V0)

NOTE: the parts listed here represent only those which go on T0-specific parts.  The gantry, toolhead, and frame can be kept stock.

#### Required

**Z drive and bed  parts**:

| Category | Part | Qty | Notes |
| - | - | - | - |
| Z Drives | NEMA14 or NEMA17 motors | 3 | For any build size, 52mm NEMA14 or 40mm-48mm NEMA17 1.8-degree steppers are ideal. Smaller (33mm NEMA14 or pancake NEMA17) and 0.9-degree steppers will be less likely to hold the bed up when the power cuts out, leading to more time needed for bed leveling, and possibly a failure to auto-level if the tilt exceeds the probing distance.  You can work around this possibility by parking the bedframe at the bottom when not in use, to get away with smaller motors.  Mix and match should be fine; use what you've got.   [Recommended NEMA17 motors](https://www.amazon.com/STEPPERONLINE-Stepper-63-74oz-Connector-Extruder/dp/B07LCK19D5/) - 39mm depth leave more internal space vs 48mm-length steppers and has plenty of hold.
| Z Drives | GT2 belt | 3x~500mm | Add 100mm for Plus size if adding Z height.
| Z Drives | GT2 16t pulleys | 3 | Z Drive pulleys
| Z Drives | MGN7H 150mm | 2 | Ideally, upgrade to MGN9C on the X carriage, then get only one of these to repurpose for a front Z drive.  See other notes below.
| Z Drives | F623 bearings | 6 | Idlers |
| Z Bed | Metal or ceramic spacers | 3 | Typically 1/2" (12.7mm) length M3 spacers or slightly longer, but it depends on your bed height, magnet height (if any), and flexplate height; 14-15mm will be needed for beds without magnets.  Holes need to be at least 3mm in diameter, but can be larger without issues (6-32, 8-32, etc). |
| Z Bed | Wago 221-412 | 6-8 | 2-position electrical connector

**Frame**

No new extrusions are required, because the original V0 bedframe 100mm extrusions are repuprosed into a new T-shaped bedrame.  Nice, huh?

**Motion**

See above for options: a medium-preload MGN9C with matching carriage is highly recommended, with an MGN7H medium-preload option not far behind.  Why mention this?  Because you don't want toolhead flop to affect bed-probe results or print quality.  

[This V0 carriage](https://github.com/zruncho3d/DuelingZero/blob/main/STLs/Low_Side_X_Carriage_x1.stl) is recommended to match.  

**Electronics**:

Two additional Z-drive stepper ports are needed.  Pretty much anything will work, and the Klipper changes are minimal.

For conversions, an added SKR Pico, SKR E3, ERCF EZ BRD, Fly-RPFmex - taped to the power supply - will work great.  The only downside is the need to update two different boards for Klipper.

If doing a larger build, much more space is available; consider starting with a 6-stepper-minimum board, such as a BTT Octopus, BTT Manta 8p, Fysetc Spider, Mellow Fly, Fysetc S6, or whatever's the latest hotness.  

The most interesting, lowest-cost option: a 5-stepper board (like an SKR 2) with a CAN bus toolhead.

**Fasteners**:

The list below almost certainly over-estimates, because it doesn't factor in screws that are freed up when doing a V0 conversion, especially for Z drives and skirt parts.  Regardless, if you get the amounts below, you should have plenty.  Recommendation: buy 50-packs of the most common screw sizes so you don't have to count or worry about it and can do the next mod without waiting for shipping.

| Category | Part | Qty | Notes |
| - | - | - | - |
| Fasteners | M2x10 self-tapping | 2 | For ZeroClick |
| Fasteners | M2x6 BHCS or SHCS | 22+ | For retaining the Z attachments in rear (2), 6-8 for the rear Z bar, nutbars (2x6), plus one per front idler (2) |
| Fasteners | M2x8 BHCS or SHCS | 4+ | For retaining the Z belt attachments in front (2x2); use this size for rear Z attachment if using printed sliders |
| Fasteners | M2 nuts | 12 | For M2 nutbars
| Fasteners | M3x6 BHCS | 47+ | For skirts (~24), bumps (16), ZeroClick probe-grab screw (1), belt attachment strengthening (6)
| Fasteners | M3x8 BHCS | 24 | bedframe extrusion connections (14), front motor mounts to motors (8?), rear motor mount vertical screws, Rear Z motor mount horizontal screws (2)
| Fasteners | M3x16 BHCS | 3 | For Z bed attachment (vertical), for Z idler tensioning (vertical)
| Fasteners | M3x12 BHCS | 4 | Rear Z belt attachment (horizontal)
| Fasteners | M3x10 BHCS | 4 | rear Z motor attachment
| Fasteners | M3 nuts | Yes | One per most M3 screws
| Fasteners | M3 heatsets | 22+ | For bed joints (3), motor skirts (4x3), rear z belt attachment (4), tensioner (1), fans skirt (2)

#### Optional
| Category | Part | Qty | Notes |
| - | - | - | - |
| Bed | Sexbolt endstop board/kit, **not soldered** | 1 | A sexbolt endstop enables Auto-Z. Optionally, repurpose the original Z endstop and use the ZeroClick probe as a virtual endstop instead. Ensure you get a non-soldered board, as the default presoldered one from DFH comes soldered to the wrong side. |
| Frame | Guitar Feet | 4 | Optional; same as used with Voron Trident.  Can use original V0.1 rubber feet instead.  Just put a nut in the foot, squeeze it, and use an M3 BHCS from the other side
| Skirts | 40mm Fans | 2 | Recommended for airflow down there.

## Build Guide

In this repo are all of the STLs needed to build a Tri-Zero Alpha which are not in another repo (primary V0.1).

All parts should be already be in print-ready orientation, with seam in the +Y dir, and no supports are needed.  Standard Voron settings, or lowered infill and fewer perims, should work fine for most parts:
- 4 perimeters
- 40% infill, depending on the part
- 0.2mm layer height

The MotorSkirts and Rear Corners are happy with 20% infill, for a bit of print speedup.

Note that you will need all the STLs in the top-level STLs folder in the quantities listed at the end of each part name, with a few exceptions:
* Between NEMA14 and NEMA17, you'll need to pick one for each motor.  You can actually mix and match them, though.
  * `Rear_Motor_Mount`
  * `Motor_Corner_Screw_In`
* For the front bed mount, pick between the main and extended one.
  * `Front_Bed_Mount` for usual V0 beds
  * `Front_Bed_Mount_Extended` for MRW-style beds which stick out by 5mm, which means they need to be shifted forwards by 5mm to expose the nozzle endstop to the nozzle.
* Front corner bumps are technically optional, but they're there by default.  You can skip them and directly add a bumper to the farthest-out screw holes with an M3 screw and nut if you'd like.  Don't worry, you won't be judged for it.

Plus, you'll want to consider these optional STLs from a few external repos:
- [No-drop nuts](https://github.com/zruncho3d/f-zero/tree/main/STLs/NoDropNuts)
- [More M2 nutbars from V0](https://github.com/VoronDesign/Voron-0/blob/Voron0.1/STLs/M2_Nut_Adapter_Rotated_x5.stl)
- [ZeroPanels](https://github.com/zruncho3d/ZeroPanels), especially Tecnologic-style ones
- [BoxZero](https://github.com/zruncho3d/BoxZero)

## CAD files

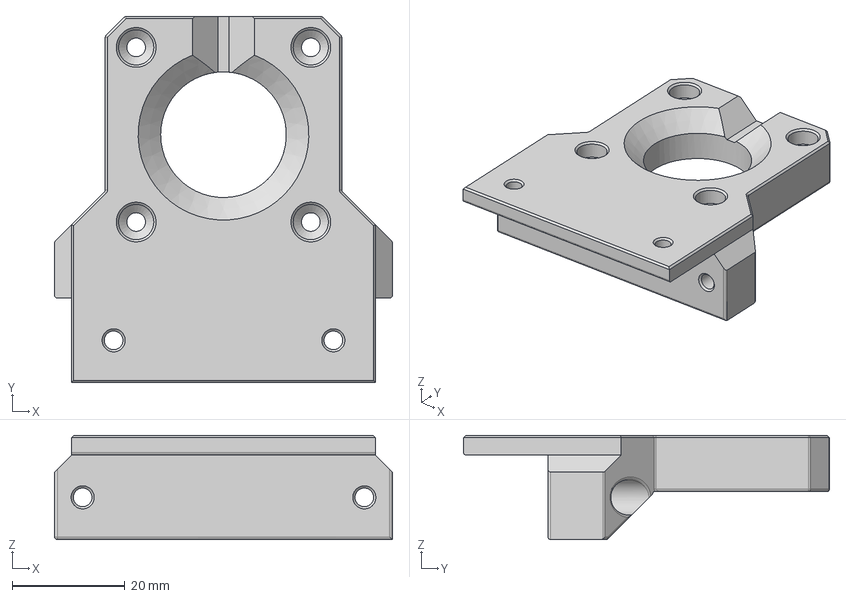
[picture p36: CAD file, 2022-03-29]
CAD/Rear Motor Mount NEMA17.step
60.0 x 65.0 x 18.5 mm

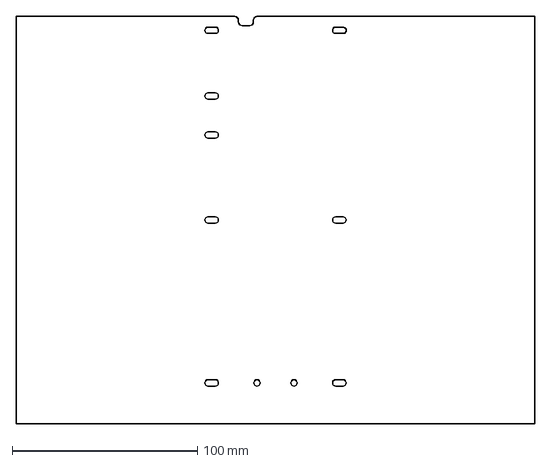
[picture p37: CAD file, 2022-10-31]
DXFs/Midplate_Plus50.dxf
280.0 x 220.0 mm

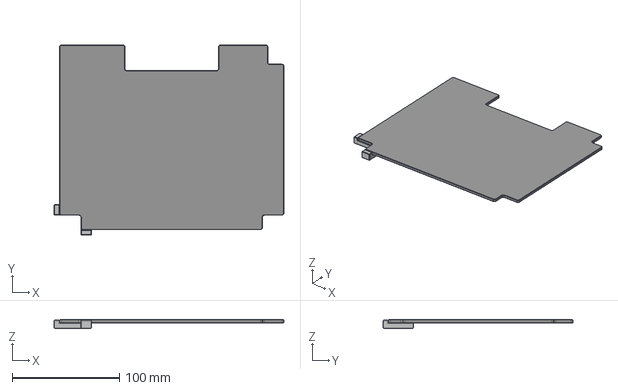
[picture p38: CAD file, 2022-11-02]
Mods/csch0/DeckPanel/CAD/Deck_Panel.step
214.0 x 177.0 x 8.00 mm

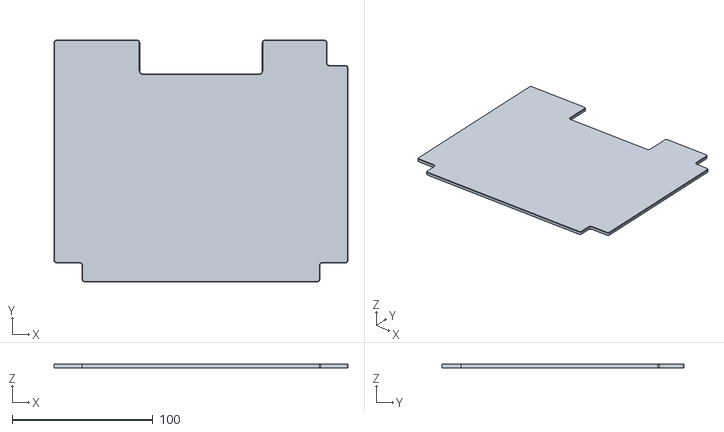
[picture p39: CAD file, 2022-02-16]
Mods/csch0/DeckPanel/STLs/Deck_Panel_x1.stl
209.0 x 172.0 x 3.00

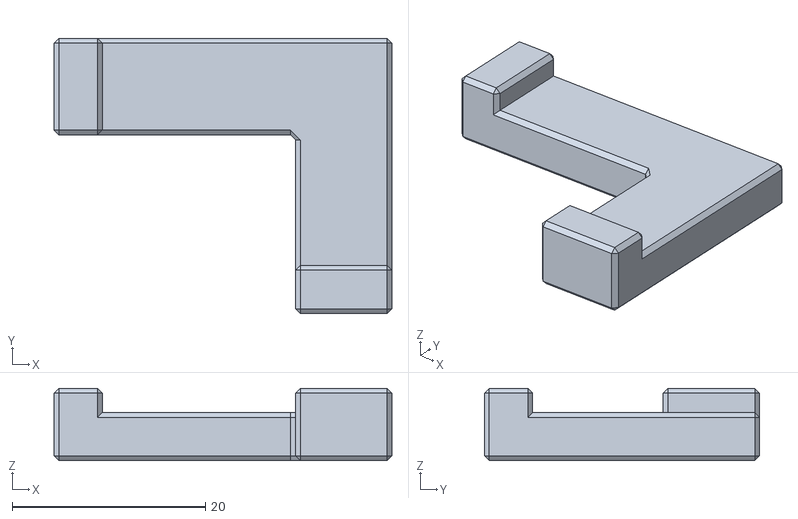
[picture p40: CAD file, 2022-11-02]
Mods/csch0/DeckPanel/STLs/Tools/Cutting_Guide_x1.stl
35.0 x 28.5 x 7.50

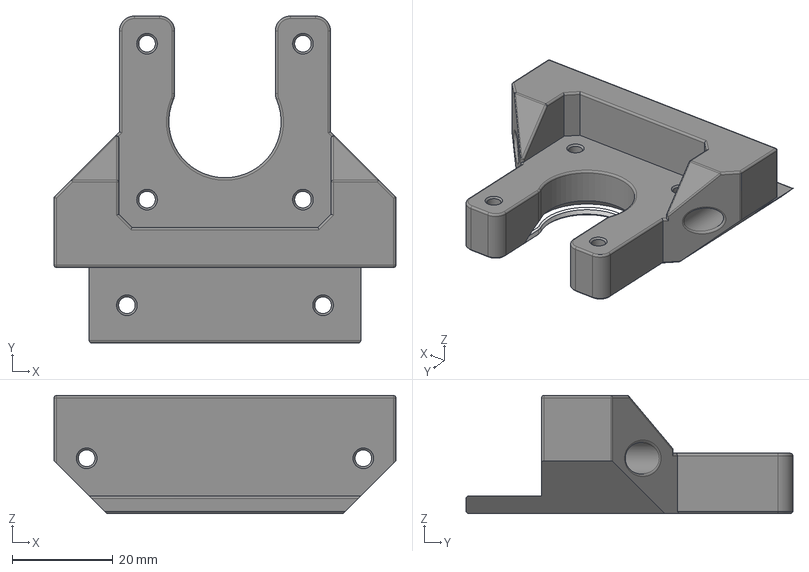
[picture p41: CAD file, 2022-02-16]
Mods/csch0/RearMotorMount/CAD/Rear Motor Mount.step
68.0 x 65.0 x 23.5 mm

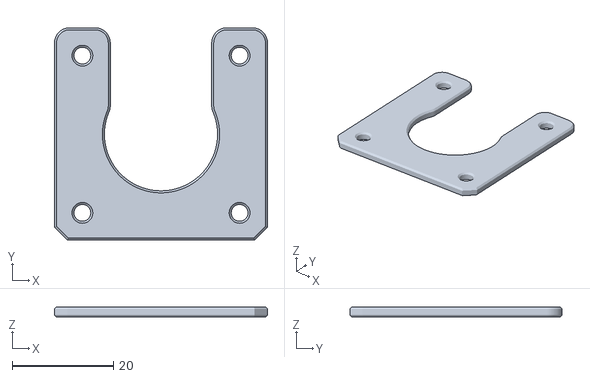
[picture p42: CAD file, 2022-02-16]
Mods/csch0/RearMotorMount/STLs/Rear Motor Mount Spacer 2mm.stl
42.0 x 41.9 x 2.00

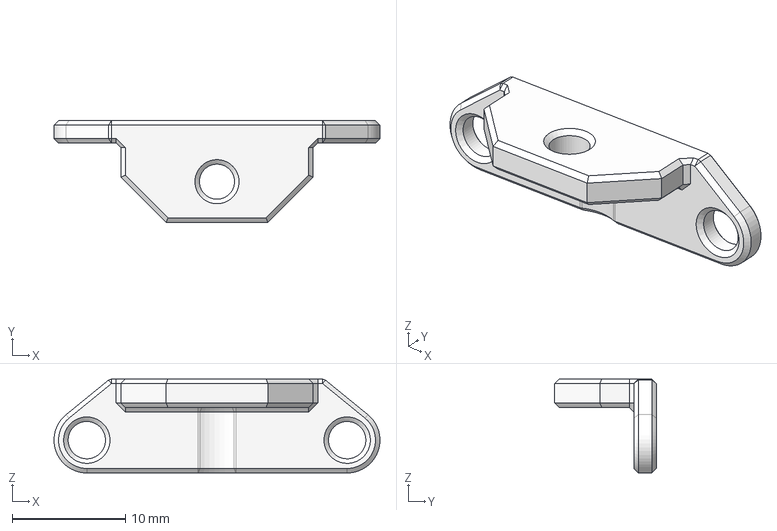
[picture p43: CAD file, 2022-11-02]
Mods/csch0/RearZAttachment/CAD/Rear Z Joint.step
28.8 x 9.00 x 8.30 mm

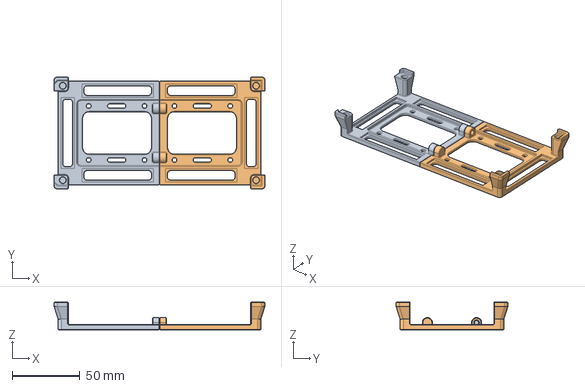
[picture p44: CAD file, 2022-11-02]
Mods/csch0/SpiderMount/CAD/Spider Mount.step
155.3 x 82.5 x 20.5 mm

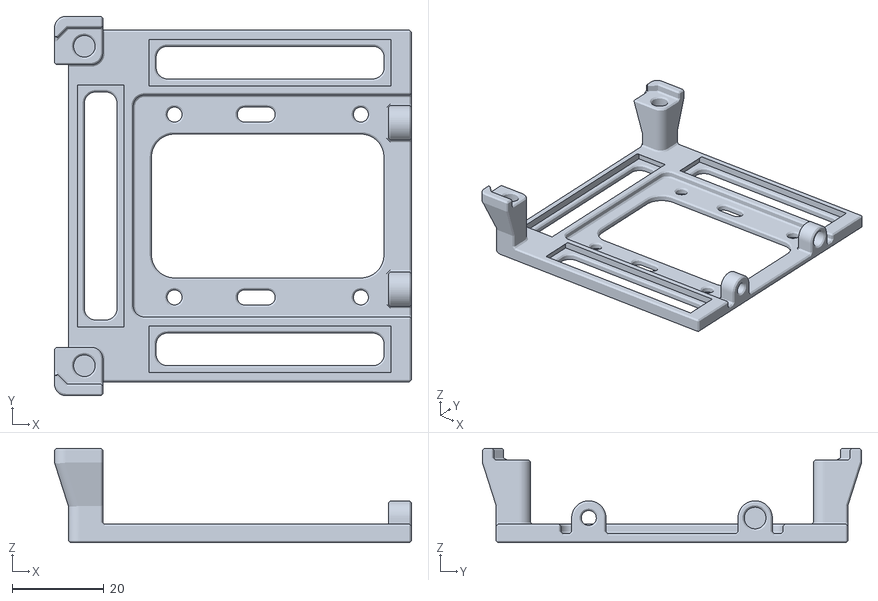
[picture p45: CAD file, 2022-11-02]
Mods/csch0/SpiderMount/STLs/Spider Mount - Left.stl
77.6 x 82.5 x 20.5

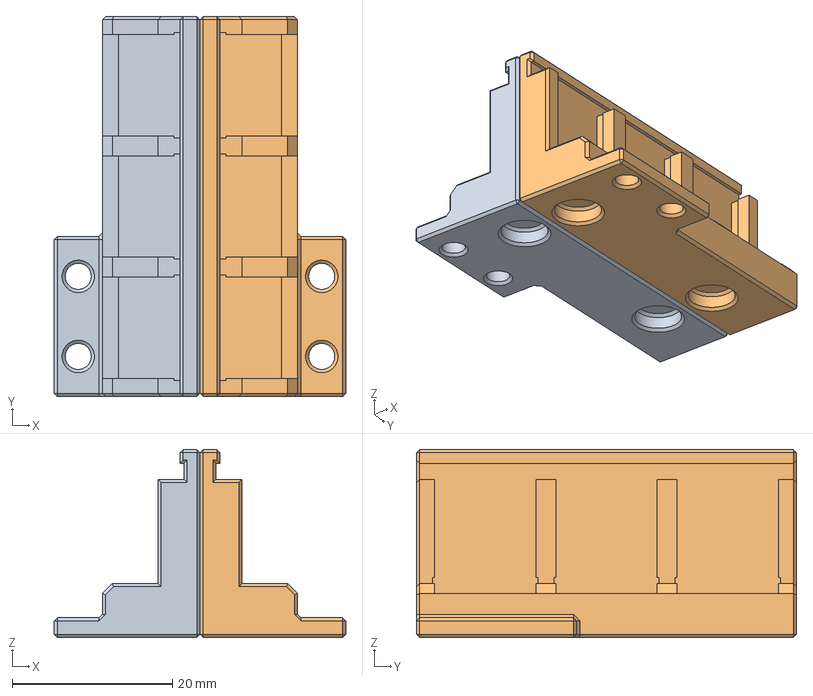
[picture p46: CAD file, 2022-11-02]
Mods/csch0/WagoMount/CAD/Wago.step
36.4 x 47.5 x 23.5 mm

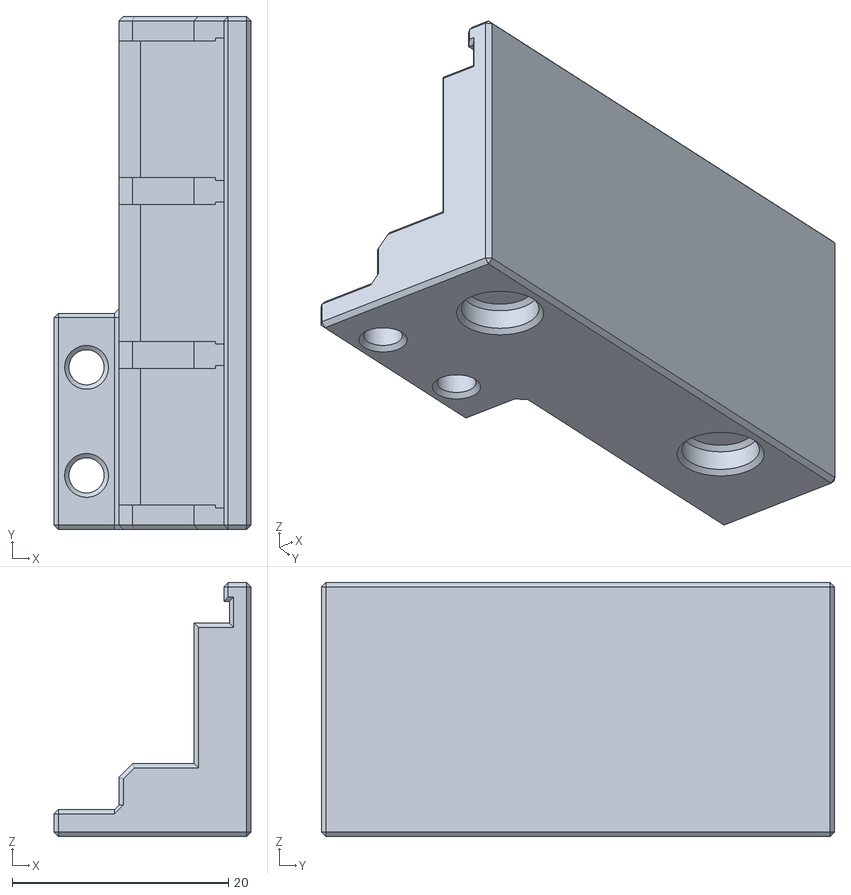
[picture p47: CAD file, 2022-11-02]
Mods/csch0/WagoMount/STLs/Wago - Left.stl
18.2 x 47.5 x 23.5

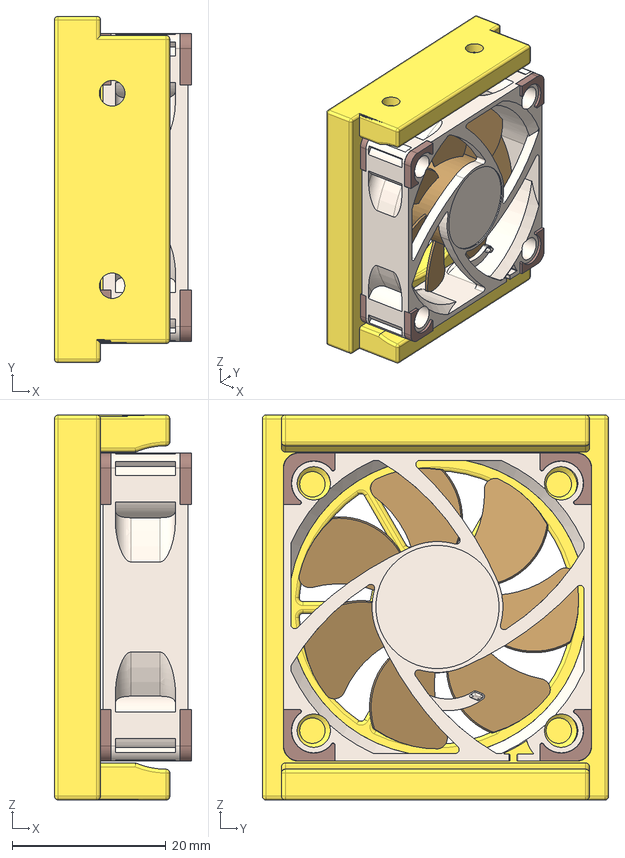
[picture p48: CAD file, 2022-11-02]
Mods/flyespresso/Motor Skirts 40mm Fan/CAD/MotorSkirts_Fan_Cover_40mm.step
17.8 x 45.0 x 50.0 mm
Noctua-NF-A4x10 v1
Noctua nf-a8-pwm fan 40x40x10 v2

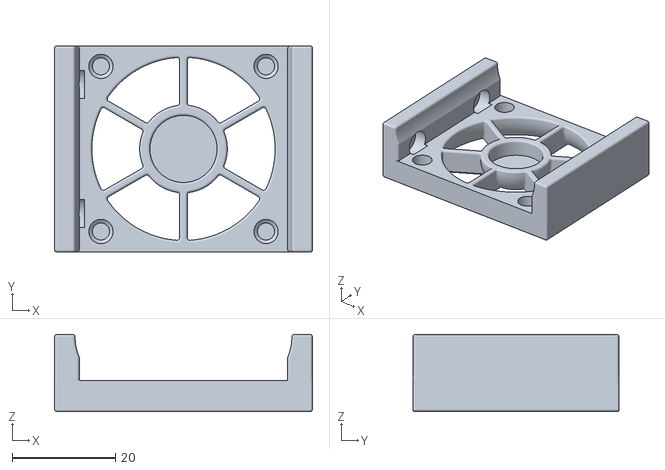
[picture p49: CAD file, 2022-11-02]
Mods/flyespresso/Motor Skirts 40mm Fan/STL/Fan_Cover_40mm_T0_Standard_x2.stl
50.0 x 40.0 x 15.0

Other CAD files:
Mods/csch0/RearZAttachment/STLs/Rear_Z_Joint_x1.stl
Mods/flyespresso/Tri-Zero-Plus-Front-Skirt-Spacers/STL/Front_Skirt_Right_x1.stl
Mods/hbo/SkirtsCollection/STLs/[a]gt2_cover_24mm_shaft.stl
STLs/experimental/ZeroPanelsMGN7H.stl
CAD/Rear Motor Mount NEMA14.step
CAD/Rear Motor Mount.f3d
DXFs/Baseplate_With_Cutouts.dxf
DXFs/Baseplate_With_Cutouts_Plus50.dxf
Mods/csch0/DeckPanel/DXF/Deck_Panel_x1.dxf
Mods/csch0/RearZAttachment/CAD/Rear Z Attachment.step
Mods/csch0/RearZAttachment/STLs/Rear_Z_Attachment_x1.stl
Mods/csch0/SpiderMount/STLs/Spider Mount - Right.stl
Mods/csch0/WagoMount/CAD/Wago Block.step
Mods/csch0/WagoMount/STLs/Wago - Right.stl
Mods/csch0/WagoMount/STLs/Wago Block.stl
Mods/flyespresso/Motor Skirts 40mm Fan/CAD/MotorSkirts_Fan_Cover_40mm.f3z
Mods/flyespresso/Motor Skirts 40mm Fan/STL/Fan_Cover_40mm_T0_Plus_x4.stl
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

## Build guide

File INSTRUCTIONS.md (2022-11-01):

# Instructions

In a nutshell: **it's not that hard**.

Even as a first-time, scratch build, it's reasonable to do the mechanical side in only a few hours.

Even if you're also doing BoxZero at the same time, the gantry can stay in place, as you work around it.

The build order isn't as prescribed as a V0, because the bedframe can be easily added and removed, and because the motors can go in before or after the MotorCorners... this is an under-appreciated benefit of T0.

**You can do it!**  Lots of people have, without even these instructions.

When in doubt, consult the CAD, but realize that not all screws and nuts are present yet.  If there's a hole that looks like it should have a screw, measure the hole depth and assume that all screws into extrusion will need 3-4mm of hidden depth.  There are almost certainly missing steps here, but these instructions are based on building 5 T0s without a manual, from memory.

And yes, the steps are a little bit high level in a few places; we'll improve these over time, with more pictures, especially.

## Prep
* **Skim the [list of PRs](https://github.com/zruncho3d/tri-zero/pulls) on the GitHub** - is there anything new and useful for you?
* Print parts per [parts guide](PARTS.md)
* Print [NDNs](https://github.com/zruncho3d/f-zero/tree/main/STLs/NoDropNuts) matched to your extrusions - more than you think you'll need.

## Pre-build
* Add heatsets where needed
  * Note that the bed attachments (3) require recessed heatsets.
* Add nuts to nutbars (one on, one off) and loosely attach rails to them
* Loosely attach pulleys to motors
* Add 2 screws to each belt-retention part (3 parts total).  They use formed threads.  Push down hard until the screw is started and keep the hexdriver aligned.  
* Build a [ZeroClick](https://github.com/zruncho3d/ZeroClick), per the instructions.

## V0 Disassembly
For conversions, of course!
* Remove the V0 Z assembly
  * .. but leave the rear verticals in place
  * Remove bedframe (possibly by removing the rail M2 screws... that's one way)
  * Take apart the bedframe, as you'll need the 100mm extrusions later
  * Remove Z railstops
  * Remove rear Z motor/stepper unit and printed mount
* Remove baseplate
  * Loosen screws on front horizontal extrusion
  * Loosen all screws on front verticals so that the baseplate can come out; you may need to loosen these screws enough to get the front verticals out.
  * Cut 20mm-wide, 15mm-deep notches on each side of the original baseplate, matching the CAD and the DXF.  Use flush cutters with ABS or a dremel or band saw with ACM.
* Remove toolhead for ZeroClick attachment
  * Frees up space to get to work, but optional.

## Build
* Ensure you have all needed screws preloaded, likely with NDNs.
* Slide rails or sliders into place
  * Loosened frame screws, plus twisting the frame, should make this possible in-place.
  * Use V0 frame alignment jig parts for rails.  
* Slide in the modified baseplate, along with the front extrusion.  
  * Corner cutouts to the front!

#### Assemble lower frame & skirt parts

* Attach MotorCorners/screws and rear corners to the frame
* Attach fan skirts to the frame
* Add motors into the MotorCorners and add 4 screws each

#### Assemble front Z parts
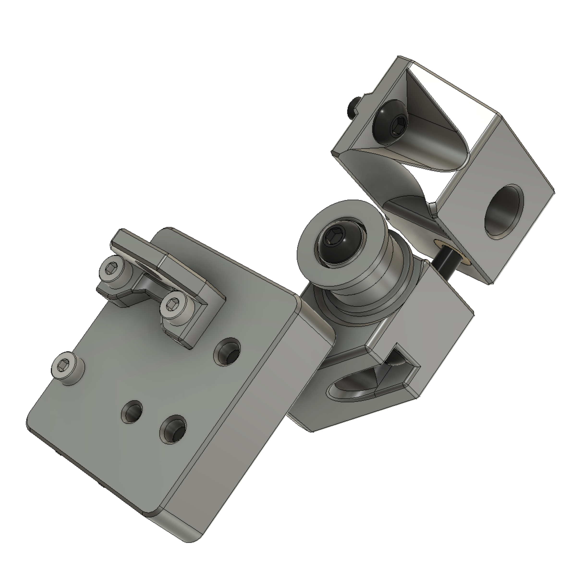
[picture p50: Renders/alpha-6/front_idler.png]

* Assemble front idlers (2)
  * Forming threads for idlers will take a little time.  
    * Ideally, add a washer on the outer end of the bearing stack (against the screw head), and tighten all the way.
* Add each Z joint assembly to each front carriage.
  * Only 3 M2 screws are needed; a shorter M2x6 goes on the bottom outer side; longer M2x8 screws are up to with the z joints.   The flat part is on top.
* Align pulleys so that belts have 0.5-1mm of clearance from the frame when tensioned. **Don't fully tighten yet.**
* Add front idler attachments; the previous railstop is removed and its nut goes to this part.  The semicircle points downward.  Another added nut goes here for the attachment, plus one below for the moving part.
* Add front idler units
  * Add a screw for locking in place and ensuring it can slide up and down; you tighten this one (against an extrusion) when the tension is set.
  * Add a screw for adjusting the tension
* Add front belts.  Attach with minimal extra belt on top first.  Then snake the belt around, past the pulley, up and to the attachment.  Leave a bit of extra to grab in the future (say, 15 teeth to start; can always trim later, and only when both sides are tensioned fully.)
* Ensure alignment for the front pulleys and lock them down.
* Tension the tensioner and ensure smooth travel across the full range of motion.
* If using printed sliders, lubricate the bearing and slide it up and down until it coats the full full extrusion travel used.

#### Assemble rear Z
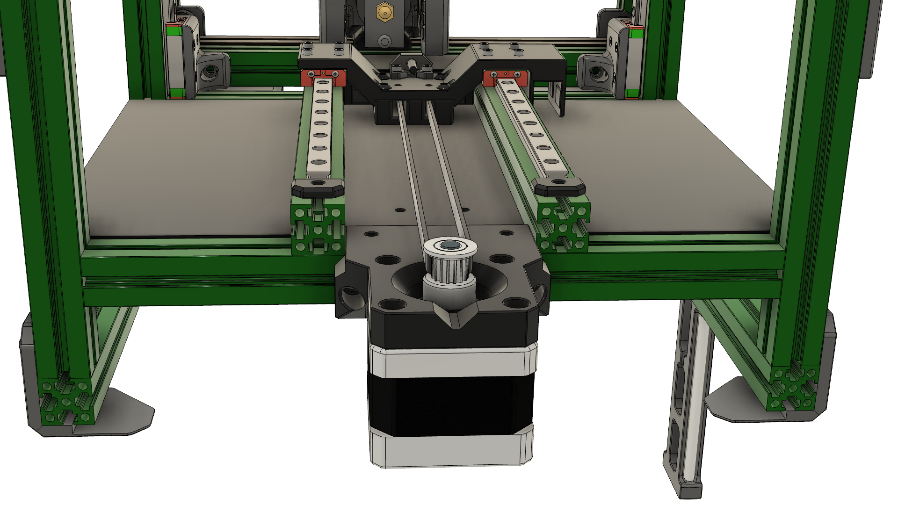
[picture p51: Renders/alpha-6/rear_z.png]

* Build rear Z tensioner unit, with screw and bearing stack
  * Run rear Z belt through it first, then add the bearing stack.
  * No washers needed; they're built into the part
* Add rear motor mount
* Add rear motor to rear motor mount
* Add rear idler top unit, which connects the two rear verticals.  Preload side screws into this one, without NDNs, then slide it down and tighten the 2 top side screws.
  * The covered side faces out and should be visible - so you won't see the tensioner at all in the correct orientation.  *Stealthy!*
* Add rear Z slider unit.  4 to 8 m2 screws are fine, with 6 preferred.  It should move smoothly.
* Add rear Z joint into rear slider.
* Attach tensioner screw and add the tensioner unit (the one with a belt already, right?).  Screw the tensioner in a turn or two - the minimum amount to keep it on.
* Route belt around lower pulley and add the rear belt attachment, with some tension applied; it'll float in place.
  * Make sure the rear belt attachment has all 4 holes aligned with the rear slider.
* Slide the belt block down, into the rear Z slider unit.  It should click satisfyingly and hold in place even without screws!
* Add screws to lock the carriage slider bar against the belt block.
* Ensure alignment for the rear pulley and lock it in place.
* Tension the rear Z belt and ensure that the motion is smooth and low-friction over the full travel.
* If using printed sliders, lubricate the bearing and slide it up and down until it coats the full full extrusion travel used.

Note: after a few times, attaching the rear Z belt becomes a ~2 min procedure.  You can do all this with the rear panel in place, because the rear wide carriage mount and the belt block can be at different heights.

#### Assemble bedframe unit
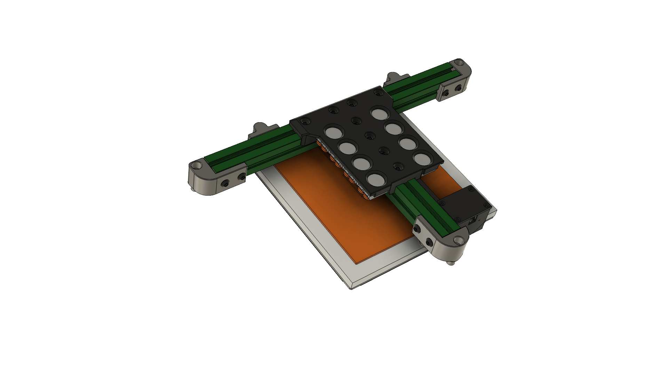
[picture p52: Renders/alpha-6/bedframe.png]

* Assemble nozzle endstop, if desired
* Add 3x100 extrusions, screws/nuts, and Wagos
* Add nozzle endstop, if present
* Add bedframe end parts (3) with screws; leave ends someone loose, as you'll align the bedframe in place later.
* Add bed spacers, bed, and bed screws.  Add loosely, align, then tighten.
* Attach bed power and thermistor wires to the Wagos.  Put high-power and low-power connections on separate sides.
* Add motor cover bumps + screws (4)
* Then add either the small bumpers or large Guitar Feet.  Guitar feet need long M3 screws into the heatsets, with a fender washer or printed spacer for each.
* Adjust all Z drives to equal, high tension.  The higher the tension, the better the printer will hold in place without power.

#### Last steps

* Add Z chain and connect wire bundle.
  * It should snap into place.  If it doesn't, size variation is the culprint.  There maybe a mod for you... check the PRs and ask on `#tri-zero` if this is the case.
* Add bedframe unit and connect to wire bundle.
* Re-add Power Supply; yes, it's tight in there, but it should just fit, with 0.5mm clearance or so.

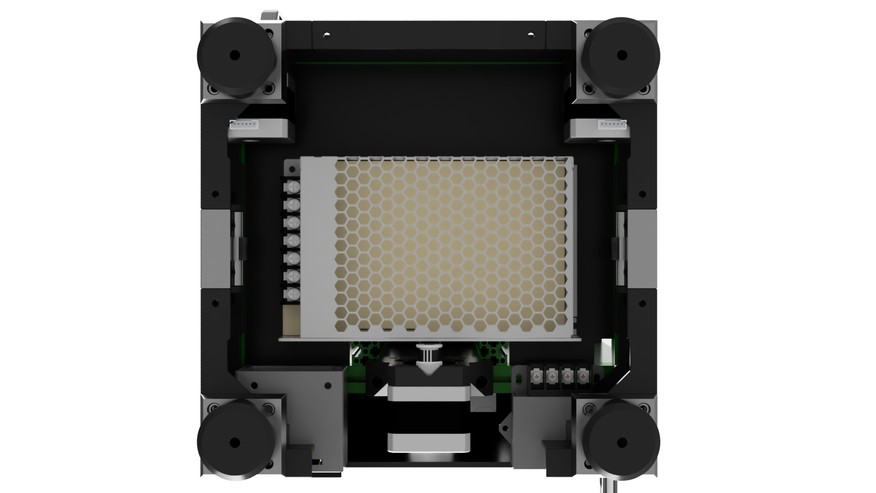
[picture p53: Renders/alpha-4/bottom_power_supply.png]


## Config/Bringup

* Do all the wiring and config to get the extra 2 ports and connect up a probe.
  * If you need a good starter config for your particular board, all Voron Trident configs are basically the same - triple-Z - so all can serve as a starting point.
* Set bed to the right height
  * You may need to adjust the length of the 3 bed-retention screws, add washers, or change bed spacers. Beds, frames, magnets,  and flexplates vary in length; 1/2" (12.7) is a good starting point, but often a few extra mm are needed.  The nozzle should just touch, with a tiny bit of extra travel available.
* Adjust Klipper config
  * However you did it... add the 2x extra Z drivers
  * Add a `z_tilt_adjust` section and configure it
  * Add a `probe` section and configure it for your probe pin
  * Add a `safe_z_home` section; should match the location of your nozzle endstop, if using one.
  * Add a virtual endstop section for the probe, if desired
  * Set up [Auto-Z](https://github.com/protoloft/klipper_z_calibration) if desired
  * Adjust max configure Z height based on a measurement
  * Add provided probe attach/detach macro or configure Klicky macros if you're using them
  * Adjust max Y if you modified the X bar
* Test probe using `QUERY_ENDSTOPS` or the page in your UI.
* Test Z motor directions using `STEPPER_BUZZ` and adjust if necessary; they should go down (+Z) first, then back up.
* Test probe attach and detach macros
* Configure Z height or tune auto-Z for a reasonable first layer
* Do dry-run print to confirm presence of probe macro
* Enjoy never having to level the bed again!!!
  * You're now able to build pretty much any printer, too, if you were able to build, wire, config, and debug this one.  Congrats!
* Post your baby's first steps to `#tri-zero` on DoomCube.   `#build-showcase` and `r/VoronDesign` are great places too.

Zruncho wants to see your build, as do others!!  They're all unique.  Really!

# Helpful Tips

* **NoDropNuts.**  Use them, especially on the frame!  But not the bedframe, as they don't add much there.  Get them from the F0 repo.  Overextrude them to fit tightly in place but still be moved with force.
* Assemble the bed frame loosely.  Screw the 3 corner-joint screws in.  THEN tighten the bed frame, so it experiences no forces except mild twisting.
* Yes, the heatsets go deep into the bed frame ends.
* Go with a beefy NEMA17 motor if possible.  Improves positioning accuracy due to more torque enabling more usable microstepping, and cheaper too.
* To get the right rear nozzle endstop position quickly, don't attach the screws to the hartk endstop board.  Get the height, THEN attach the screws.  Much easier to adjust the height this way.
* Share your progress on `#tri-zero`.  It's really motivating to see everyone's creations and learn from them.
* **Just do it.**  There is no lower-cost way to get ABL on your V0, especially for fresh builds.  Even if you don't care about ABL, the build is more straightforward.

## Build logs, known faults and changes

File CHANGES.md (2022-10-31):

### 2022-10-16 Update:

Alpha-6.

It's about time.  Plus50, new parts, doc updates.  Details in main page.

#### 2022-04-18 BoxZero is out!

BoxZero is a T0 spinout. It doesn't require T0, but works great with it.  The tagline:

> Simplify, strengthen, and seal your Voron Zero or V0-derived printer (Tri-Zero, Double Dragon) by ditching the tophat and moving to a full-box frame.

[Check it out here](https://github.com/zruncho3d/BoxZero).

#### 2022-02-16 Update: $#!+ Just Got Real

**(1)** We have our first Voron-serial'ed Tri-Zero!  Congrats to Red5, whose black-and-blue Tri-Zero looks great and prints great:

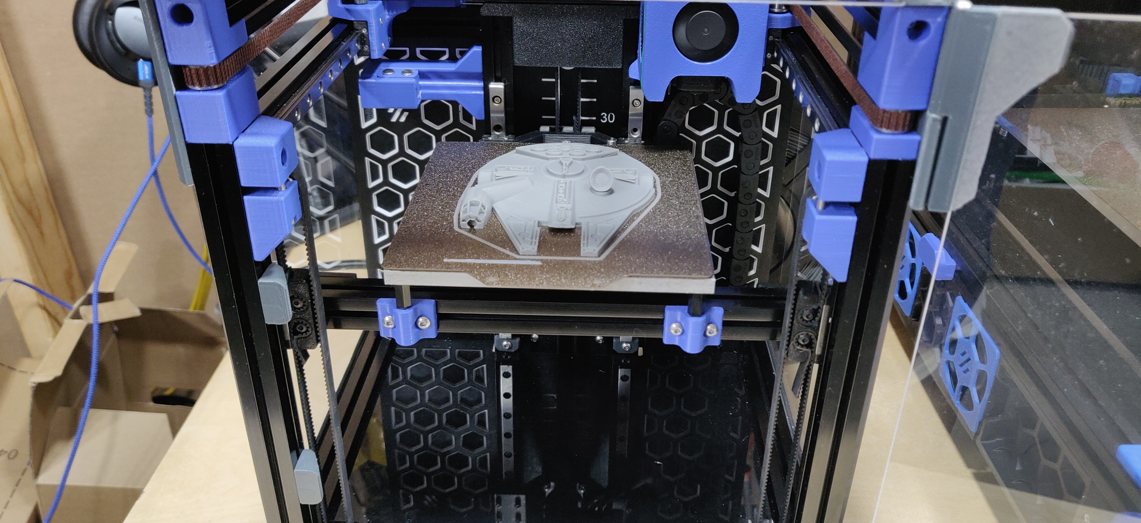
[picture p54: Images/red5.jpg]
Red5
  

Definitely check out the [serial request video for V0.1382](https://www.reddit.com/r/voroncorexy/comments/simwer/trizero_t0_serial_request_v01_red5_8573/) to see what this T0 looks like, printing.  Red5 reports:

> So far no issues at all with the layers...  I also have printed a few 120mm tall items with perfect vertical layers.

Yes, direct-drive 1.8-degree stepper motors work great in this application!  We can get away with no reduction when the bed assembly is only ~500g, unlike printers with ~1800g flying gantries.  Direct drive is simpler, more reliable, and lower-cost.

**(2)** We have our first merged Pull Requests!  Props to csch, who contributed 3 different parts in the new Mods folder.

**(3)** We have our first complete release, in Alpha-5!  This includes many new or improved parts:

**New:**
* [ZeroClick](https://github.com/zruncho3d/ZeroClick) is out now, and is the default bed-probing solution for T0.  You don't need to reprint your MiniAB shroud.

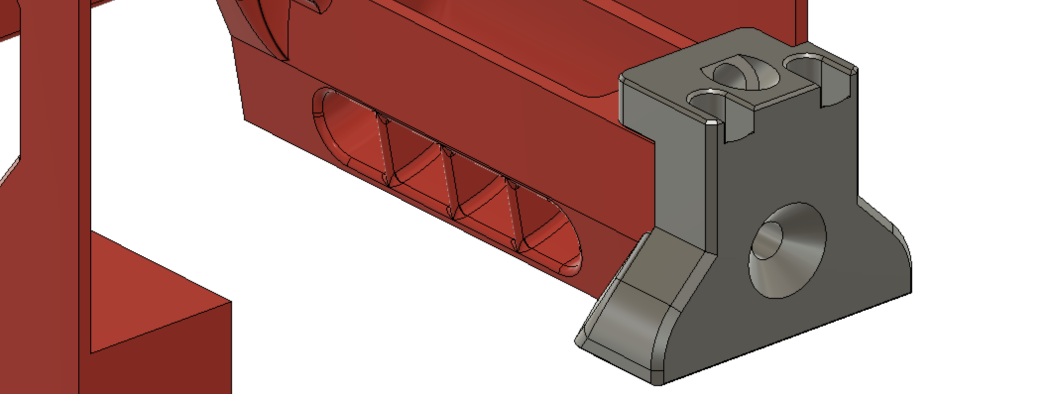
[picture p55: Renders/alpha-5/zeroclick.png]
Zeroclick
  

* [ZeroPanels](https://github.com/zruncho3d/ZeroPanels) are spun out now, and are the default enclosure solution for T0.  Prints in < 2 hrs and pops on and off.
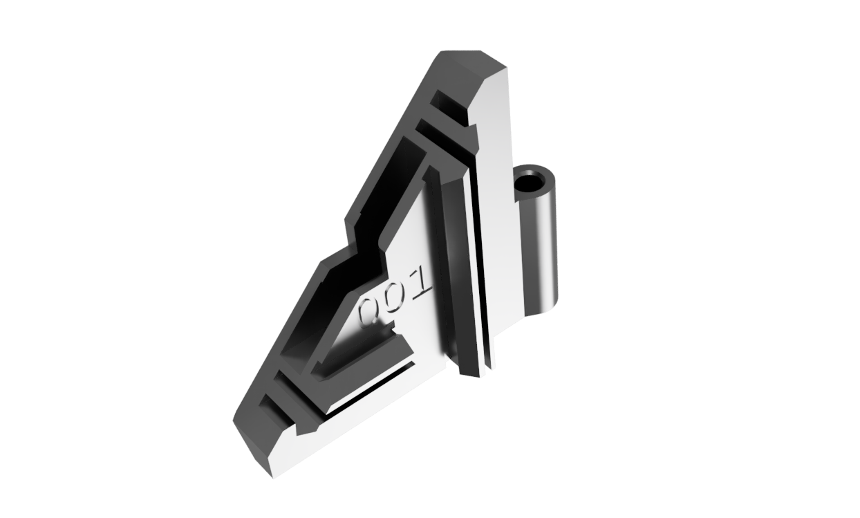
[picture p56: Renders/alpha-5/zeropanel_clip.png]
  
* New rear corners are in:

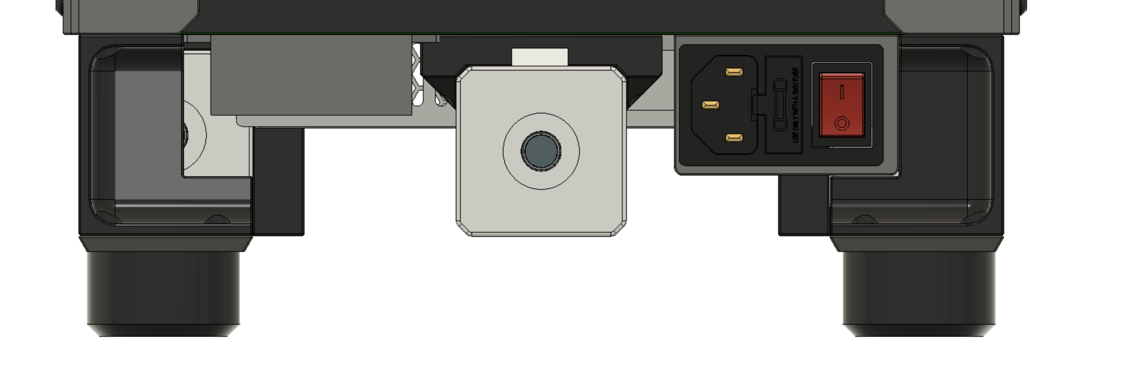
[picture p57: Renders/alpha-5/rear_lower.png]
Rear Lower
  
  Smaller, stronger (since they mount to the frame crossmember), and now you can reuse your V0.1 inlet.

* [4.3" Waveshare Touchscreen](https://www.amazon.com/dp/B088JTD6JN) mount added: a great way to add [KlipperScreen](https://github.com/jordanruthe/KlipperScreen), which keeps getting better.  Based on Jeoje's great Voron2.4 [Touchscreen mod](https://github.com/VoronDesign/VoronUsers/tree/master/printer_mods/jeoje/4.3_Inch_Touchscreen_Mount), but adapted to fit securely in a 1515 extrusion.

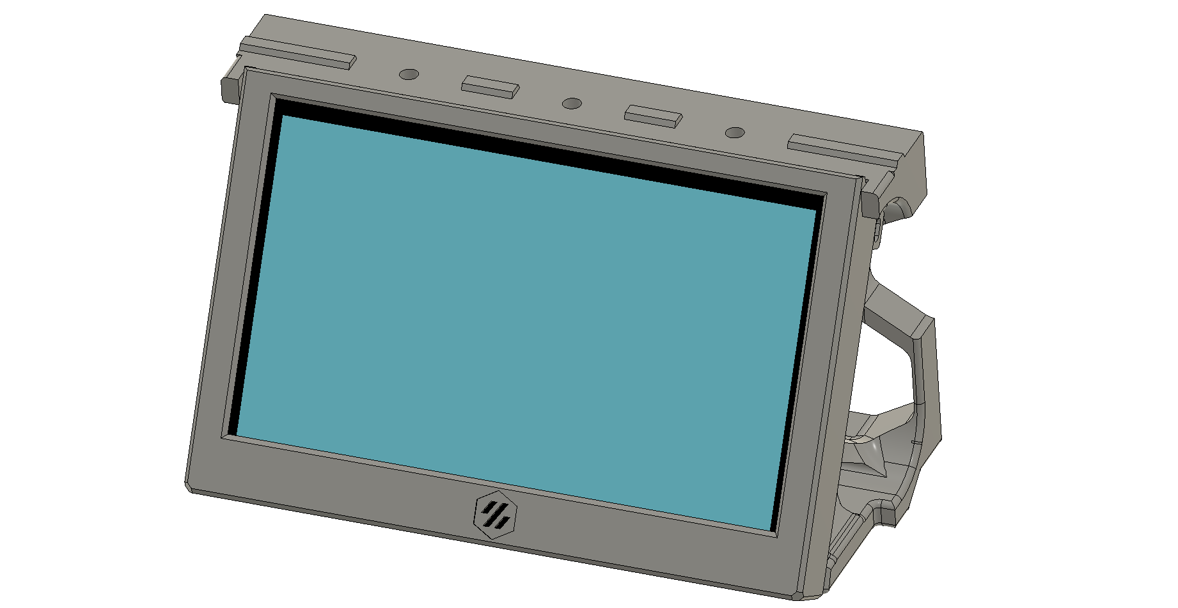
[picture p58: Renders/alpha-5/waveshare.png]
  

* [Mini 12864 Display](https://deepfriedhero.in/products/mini-12864-display) mount added: a super-affordable way to get a display you can easily read from a distance.  Based on Gola's [V0 Trident Skirt Mix](https://github.com/VoronDesign/VoronUsers/tree/master/printer_mods/golas/v0-trident-skirt-mix), but sized to fit T0.  You don't need the printed corners or guitar feet on your T0 with this one; instead, you can carry over the bumpers from a V0.1.

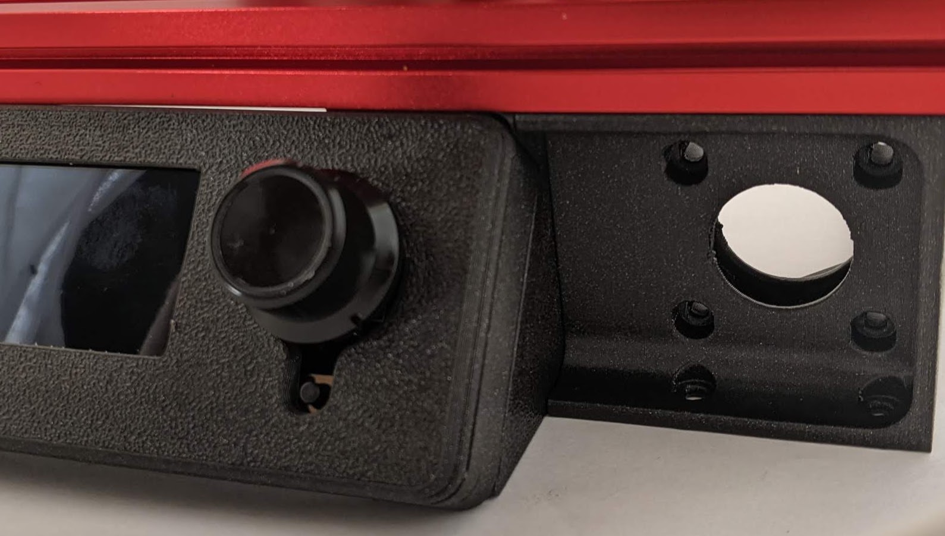
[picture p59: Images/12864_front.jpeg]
Front
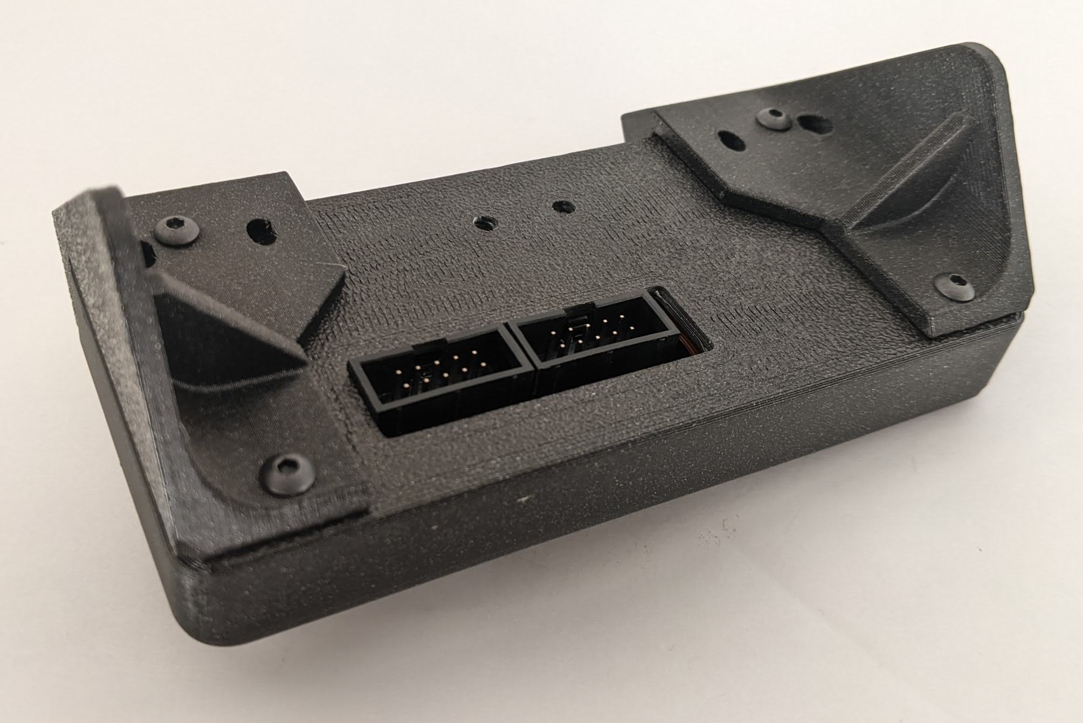
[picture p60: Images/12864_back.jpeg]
Back
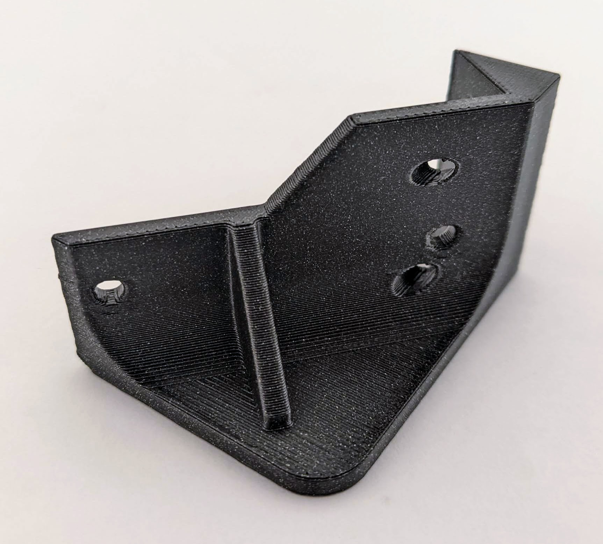
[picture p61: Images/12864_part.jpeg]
Part
|  |  |  
| - | - | - |

**Improved:**
* The Z Nozzle Endstop is now rear-mounted;
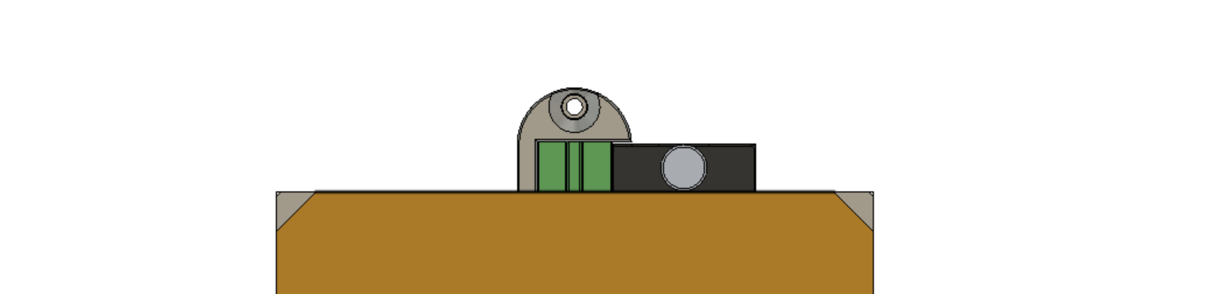
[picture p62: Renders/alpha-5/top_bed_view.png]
Top Bed


  Modified Rear Bed Mount and Front Bed Mounts have been added to match it.  You'll lose a few mm of rear Y travel, but the positioning works much better with [Double Dragon](https://github.com/zruncho3d/double-dragon), where it enables automatic toolhead offset calibration and wider beds.
* The Rear Z Mount is now taller:

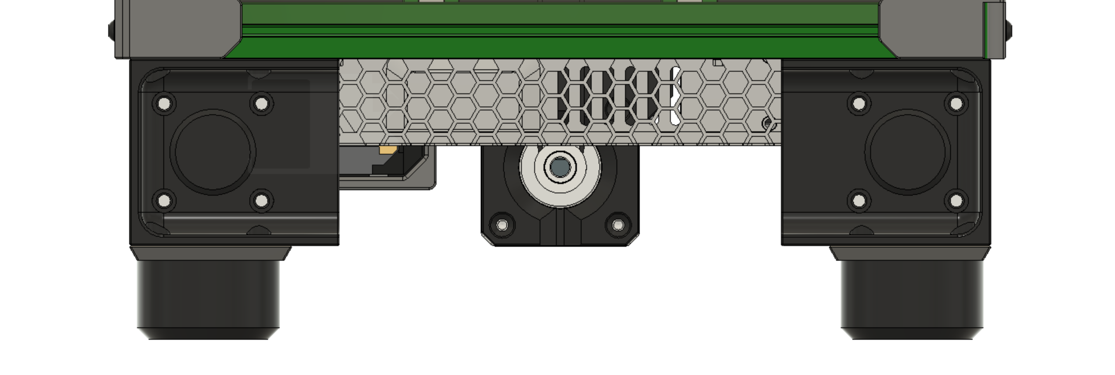
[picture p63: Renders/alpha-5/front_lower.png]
Front Lower
  
  This provides 3 real benefits:
  * Motors (whether NEMA14 or NEMA17) with long shafts no longer conflict with the power supply.
  * Z motors can be removed now, even with the mount in place, as there's more clearance from the power supply for the allen wrench to get in there.
  * Your T0-in-progress can sit flat with only 3 below-deck parts: 2x MotorCorners and one Rear Z Mount.
* Front MotorSkirts now have larger cutouts to fit motors with JST pins... like mine.

What's coming next?  More community contributions, more size options, and more QoL upgrades.  Maybe even a beta release... it's starting to stabilize.  (Famous last words, you say).

As usual, all parts have been pre-oriented for easier printing, and the CAD has been updated.  Enjoy!

#### 2022-02-08 Update
* [ZeroClick](https://github.com/zruncho3d/ZeroClick) is out!  Fast & simple bed probing for tiny printers... like Klicky, but sized right.  The default now for Tri-Zero.  Actually, ZeroClick is a T0 spinoff proect, just like ZeroPanels, but since both have much broader relevance to more V0-ish printers, they live in other GitHub repositories.

#### 2022-01-23 Update
* [ZeroPanels](https://github.com/zruncho3d/ZeroPanels) are out!  These provide an option for easily enclosing your T0, while providing the additional gap needed to enable the carriages to stick out of the frame.  They pop on and off in seconds and reuse your clear panels and front printed parts from a V0.

#### 2022-01-20 Update
* T0-Alpha-4 released, with 11 new parts.
* **Now supports NEMA14 and NEMA17**: use what you've got!
  * The new MotorSkirts push the motors as far out as possible, freeing up enough space to fit larger power supplies  more easily (between motors or against the motor rear plates).  
  * The front skirt can be swapped for a [4" touchscreen mod](https://github.com/Fleafa/VoronUsers/tree/V0.1-Trident-skirt/printer_mods/roboticator24/4inch_touchscreen_mount_for_v2.4) for [KlipperScreen](https://github.com/jordanruthe/KlipperScreen).  
  * Guitar Feet (4x) can be added to give a nice handle with the skirts... or, retain the original V0 bumpers.
* New rear motor mount: now, mounts to the nuts you'd already have on a V0 if doing a conversion.  This is a huge deal!  To convert a V0, you no longer need to dissassemble the rear frame.
* New clip-in 30mm fan mounts on the sides for side-to-side airflow.
* New clip-in front motor pulley covers.  Leave them out if you want to see Z motion or put some spinners on.
* Slightly thinner rear Z idlers: now they fit within the extrusion thickness of 15mm.  Two benefits: more space for a probe back there (hint, hint) and now the center tensioner fits a regular 12mm BHCS, so no cut screw or washers are needed anymore.
* CAD and STLs for alpha-4 are now available.  The original V0.1 bed assembly is gone, for a smaller file size, but Fusion is failing to export, so .step only for this one.
* Want to contribute?  PRs would be welcome for these improvements:
  * Integrated probing solution
  * Rear side skirts with less material.  Duplicating the front skirts adds unnecesary material and gets in the way of a rear outlet.  I got tired and chose to release this instead of modding the skirt.  Other improvements matter more.
  * Integrated bed Wago mount (5x2)

#### 2022-01-16 Update:
Initial BOM posted below.  No large changes are expected, but no promises are made w/an alpha!

#### 2022-01-11 Update:
* T0-Alpha-3 released: **now with less!**
* **Now Direct-Drive** - yes, this is a huge change.  Frees up space, lower costs, and speeds up the conversion time.  And yes, regular NEMA14 motors seem to have just enough unpowered hold and enough resolution to make this work in practice.  Long (V0.1-spec) NEMA14s should be overqualified to hold the bed when the power cuts out.
* **Now using MCMBen Trident-style skirts** - these look great and enable integrated side skirts with motor mounts.  Only needs one part and its mirror to change, the front corners, to add clearance for the front belt pulleys.  See the repo for these.
* Simplified Z attachments: easier and faster to print, increases Z travel (122mm out of the box), and also removes 6 M2 screws.
* New rear motor attachment piece.  It's basically a block.
* Updated front idlers: reduces the material needed and slightly increases clearance for another mm of X travel.
* CAD and STLs for alpha-3 are now available.  GitHub limits files to 100 MB and the Fusion export is just a bit too large.  [Go here for the Fusion export](https://drive.google.com/file/d/1fiEJLRE4qYLFB2CRu8r5_06jv_Fr14W6/view?usp=sharing).
* What's coming next?
   * Redone integrated skirts.  The motors are too far inboard now, which wastes space and loads the motor bearings unnecessarily.  This was intentional, to minimize skirt changes, but if we go full-custom with the skirts, they can be more optimized for Tri-Zero.  For example, by extending beyond the frame boundary - to the enclosure boundary - it should be easier to enable NEMA17 motors.
   * A probing solution is coming, called ZeroClick, but it needs a corresponding dock created before release.
   * A rear Z motor mount that doesn't change the nut locations relative to V0.1 would be nice!
   * Lessons from Double Dragon point the way to probably 130mm Z (!) using the same rails.
   * ZeroPanels are coming soon: screwless, nutless, magnetless, toolless enclosure panels that attach and remove in seconds.
   * Maybe... just maybe... a block-and-tackle Z for 2x resolution and torque.
   * Some built-in solution for mounting Wagos under the bed.

#### 2021-11-15 Update:
* T0-Alpha-2-Green can **reliably** and automatically level itself.  Config coming soon.
* The new flexure joints beat the KGLM03 joints in smoothness, as they converge *very* quicky when doing automatic leveling, plus drop a few bucks from the cost total.
* Z has been increased to right about 120mm, and nearly all main Z motion parts had to change to enable this.
* Front idlers were narrowed a bit to avoid a tiny bit of interference in the very front of the printer.  
* CAD and STLs for alpha-2 are now available.   
* What's coming next?
  * Lessons from alpha-2 will lead to a much simpler alpha-3, likely with even taller Z (beyond 120mm).
  * Different detachable probe options are under testing, including SideSwipe and a stretched Klicky-style probe.

#### 2021-11-07 Update:
* T0-Alpha-1-Green can automatically level itself, as of today!  Images and video proof are availabe on Discord.  Real life nearly matches the CAD.
* CAD and STLs for alpha-1 now available.

## Older updates

* 2021-11-07: Alpha release now up on GitHub.
* 2021-11-06: First successful triple bed leveling, after designing a whole bunch of parts.
* 2021-11-04: After focusing on F-Zero for awhile... we’re back.
* 2021-08-15: Zruncho’s F-Zero-Black torn down to provide parts for Tri-Zero-Proto.
* 2021-08-15: Now using spherical joints.  After some discussion on #tri-zero, going to go with simple spherical joints to start, just like the announced-today Voron-Trident - a triple-Z Voron 1.8 follow-up.  If it’s good enough for that printer, it should be good enough for a much smaller printer.  Kinematic mounts can come later.  
* 2021-08-14: The unofficial DOOM-Stream went well.  Now we have a CAD!  Not complete, but still useful.  Major contributions from `l.e.o.p.a.r.d`, `Ericsson`, `Kayos Maker`, and many others on the call, to figure out how to make this happen, and whether it makes any sense at all.
* 2021-08-14: ``#tri-zero` on DoomCube Discord created - this is where design discussion will live.

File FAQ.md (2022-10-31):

## FAQ

### What do you mean by Alpha Release?

The parts actually work, the design is relatively stable, and you can build an awesome printer here.  

But the parts may change.  

### What is missing in the Alpha Release?

As of Alpha-6, nothing *critical* is missing.

However, in the future, these are likely improvements:
* improve bottom and rear sealing
* improve Z chain mount for easier printing and easier customization to different-size chains
* more docs and sample configs

### What extrusions do I need?

NONE!  V0 bed extrusion (3x100) are repuprosed.

### Does this mod mix well with the Kirigami mod?

Not at all.  

Kirigami is a more rigid cantilevered bed.

Tri-Zero eliminates the cantilever flaw, and adds automatic bed leveling.

### Is it true Tri-Zero can print better than a regular V0?

Yes, for at least two reasons:

(1) Perfect bed leveling improves print reliability and can improve edge quality near the bottom.

(2) Compared to a flying gantry printer, there's less potential for ringing, because the part that changes directions - the toolhead - is not suspended with rails.  Only the bed is.  Zruncho's interested to get more data here.

### Is a Z nozzle endstop really a requirement?

**No, it's not.**  The disadvantage (Zruncho's opinion here) is that nozzle endstops can read differently when there's oozed filament on them, and you only need a small amount of error (0.05mm) to really mess up bed leveling.  If you don't have active nozzle cleaning before nozzle probing, this is a risk.  And the nozzle endstop add a little cost.

But, Auto-Z is pretty awesome.  You can change nozzles and plates and do nothing and it'll just work.

And - really useful - for IDEX machines you can use the nozzle endstop to calibrate the height between the two nozzles, painlessly.

Point is - it's up to you, just like everything else on your T0.

### What if I have questions?

The full docs here, along with the CAD, should answer most questions.

Still stuck?  Go to the [DoomCube Discord](https://discord.gg/doomcube) and search for a related Q on #tri-zero-forum.

If you can't find anything, ask on #tri-zero-forum, or if not a Q, on #tri-zero.  This is an active channel and the best way to get support.  Make sure to add the relevant details so someone has the context to help you.  What did you try?  Where did you look? Did you look at the CAD?  There’s an active community... if your question doesn’t get a response within two day, repost it.  

DO NOT ping Zruncho... or at least, save your ping for when you're really stuck.

Enjoy your T0!!!

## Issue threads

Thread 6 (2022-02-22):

Increase default height of bed spacers to fit MRW beds and shorter nozzles

zruncho3d, 2022-02-22:
Reported by hyjacked on Discord - thanks!

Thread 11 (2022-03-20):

Feature Request: Increase size of rear Z tensioner to improve strength

zruncho3d, 2022-03-20:
This part started as a mod to MCMben's block-and-tackle Z, which is more space-constrained.

Bumping up the width of that part to account for prints done with less-than-optimal layer adhesion seems like a nice improvement.

zruncho3d, 2022-11-02:
The issue was improper print orientation, which was fixed with alpha-6.  Closing until there's evidence of any future failures.

Closed 2022-11-02.

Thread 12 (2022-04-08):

Improvement: increase resilience of bed joints

zruncho3d, 2022-04-08:
Multiple reports so far of cracked bed joints, including ones broken by TheMrFish and others.

I haven't personally experienced a failure yet, but I print warm/hot in a heated chamber with known-good ABS.

zruncho3d, 2022-10-31:
Resolved in alpha-6: turning the print 90 degrees, so the perimeters flex, should provide plenty of strength.

Closed 2022-10-31.

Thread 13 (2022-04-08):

Feature Request: Add files for baseplate with cutouts for belts

zruncho3d, 2022-04-08:
Makes sense... avoids annoying cuts, especially for those going with ACM panels.  Those buying and then modifying off-the-shelf ABS panels for V0.1 can just use flush cutters, but this is worth adding.

zruncho3d, 2022-10-31:
Resolved in alpha-6, for both standard and plus sizes.

Closed 2022-10-31.

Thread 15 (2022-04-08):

Improvement: Move from clip-in to screw-on front motor pulley covers

zruncho3d, 2022-04-08:
Would be stronger and less sensitive to layer bonding.

zruncho3d, 2022-11-02:
Resolved with alpha-6.  Woo!

See STLs:
https://github.com/zruncho3d/tri-zero/tree/main/STLs

Closed 2022-11-02.

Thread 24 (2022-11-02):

Improvement: More-easily-tweaked Z chain mount

zruncho3d, 2022-11-02:
Issues:
* The rear spacer bar is a long, skinny print, which can be difficult without an enclosure.
* The end doesn't fill all z chains, apparently.

Suggestion is to split it into two pieces for easier printing an easier customization.  Presumably two pieces, with the usual heatsets and m3s, is the way to go.

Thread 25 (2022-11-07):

wrong Extrusion length for rear of bedframe for new build

madejackson, 2022-11-07:
I'm not sure but I believe this should be 150mm instead of 100mm:

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

shahfil, 2022-12-26:
Rear Horizontals, 3x 50+100 joined (no color) - not presenting in new build too.. I need 3x150 or 3x250 length?

iridium13, 2023-02-10:
I don't think either one is correct.  Step file has....
- 15 250mm
- 4 400mm
- 1 150mm

The plus50 render also shows 2 additional 250mm lengths on the sides above the belts.

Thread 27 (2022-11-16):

Add ref to X carriage part, once moved

zruncho3d, 2022-11-16:
Currently here

https://github.com/zruncho3d/DuelingZero/blob/main/STLs/Low_Side_X_Carriage_x1.stl

mjrider, 2023-10-22:
the carriage doesn't seem to be there anymore

Otann, 2024-07-07:
> the carriage doesn't seem to be there anymore

It's here now, but it seems it is for 0.1

https://github.com/zruncho3d/DuelingZero/blob/main/Archived_v1/STLs/Low_Side_X_Carriage_x1.stl

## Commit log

2021-11-07 Alpha Release + first commit
    [rear_z_attachment_x1.stl, rear_z_belt_attachment_x1.stl, rear_z_idler_x1.stl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]
2021-11-16 Alpha-2 release
    [bed_center_brace.stl, front_bed_attachment.stl, front_bed_attachment_mirrored.stl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]
2021-11-16 Reorient rear z belt attachment
    [rear_z_belt_attachment_x1.stl]
2021-11-16 Add experimental probing parts
    [longklicky_mount.stl, sideswipe_probe_press_tool.stl]
2022-01-12 Alpha-3 Release - now direct drive
    [corner_front_left_x1.stl, corner_front_right_x1.stl, front_bed_attachment.stl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]
2022-01-16 Add BOM
2022-01-20 Renames to Capital_Case to match V0 repo
    [Bed_Center_Brace_x1.stl, Corner_Front_Left_x1.stl, Corner_Front_Right_x1.stl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]
2022-01-20 Alpha-4 Release - ~11 new parts and NEMA17 support
    [Corner_Front_Left_x1.stl, Corner_Front_Right_x1.stl, Front_Skirt_x1.stl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]
2022-01-28 Note location of bed spacers from F-Zero repo
2022-02-13 added base panel
    [Deck_Panel.step, Deck_Panel.stl]
2022-02-13 added read motor mount
    [Rear Motor Mount Spacer 2mm.stl, Rear Motor Mount.step]
2022-02-14 added Rear Z Attachment
    [Rear Z Attachment.step]
2022-02-16 Alpha-5 Release: ZeroClick, ZeroPanels, corners, and more
    [12864_Mount_Mirrored_x1.stl, 12864_Mount_x1.stl, Front_Bed_Mount_Extended_x2.stl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]
2022-02-17 added cutting guide and dxf
    [Cutting_Guide_x1.stl, Deck_Panel.step, Deck_Panel_x1.dxf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]
2022-02-17 A liiiiiiittle more than 450mm is needed for each belt
    Bump to 500mm to be sure though.
2022-02-18 added rear z joint
    [Rear_Z_Attachment_x1.stl, Rear_Z_Joint_x1.stl]
2022-02-18 added cad
    [Rear Z Joint.step]
2022-02-23 added readme and STLs
    [Wago - Left.stl, Wago - Right.stl, Wago Block.stl]
2022-02-26 added spider mount
    [Spider Mount - Left.stl, Spider Mount - Right.stl, Spider Mount.step]
2022-02-26 added cad and images
    [Wago Block.step, Wago.step]
2022-03-01 Initial Release of Fan Skirts
    [Fan_Cover_40mm_T0_Plus_x4.stl, Fan_Cover_40mm_T0_Standard_x2.stl, MotorSkirts_Fan_Cover_40mm.f3z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]
2022-03-01 Print Orientation Fix
    [Fan_Cover_40mm_T0_Plus_x4.stl, Fan_Cover_40mm_T0_Standard_x2.stl]
2022-03-01 Initial Release
    [Front_Skirt_Left_x1.stl, Front_Skirt_Right_x1.stl, MotorSkirts_Front_Skirt_Plus_x1 v6.f3d]
2022-03-29 Add Rear Motor Mount CAD files
    [Rear Motor Mount NEMA14.step, Rear Motor Mount NEMA17.step, Rear Motor Mount.f3d]
2022-07-25 README.md: clarify optional second endstop
2022-07-25 README.md: further clarify endstop board.
2022-08-26 Add MGN7H sliders
    [ZeroPanelsMGN7H.stl]
2022-09-21 Minor rename
    [[a]_Front_Corner_Bump_Mirrored_x2.stl, [a]_Front_Corner_Bump_x2.stl]
2022-10-31 Alpha-6 Release: Plus50, Sliders, doc redone, & more
    [Baseplate_With_Cutouts.dxf, Baseplate_With_Cutouts_Plus50.dxf, Bed_Center_Brace_x1.stl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]
2022-11-01 Initial load pull request
    [[a]Skirt_Bottom_Plates_x4.stl, [a]Skirt_Fan_Mount_x2.stl, [a]gt2_cover_20mm_shaft_x2.stl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]
2022-11-02 Put @hbo's skirt collection into a folder
    [[a]Skirt_Bottom_Plates_x4.stl, [a]Skirt_Fan_Mount_x2.stl, [a]gt2_cover_20mm_shaft_x2.stl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]
2022-11-03 Clarify spacers
